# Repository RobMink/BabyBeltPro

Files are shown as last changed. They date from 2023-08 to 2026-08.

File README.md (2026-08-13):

# BabyBeltPro
BabyBelt Pro (V2.6, see branches for V1, V2, or v2.5)

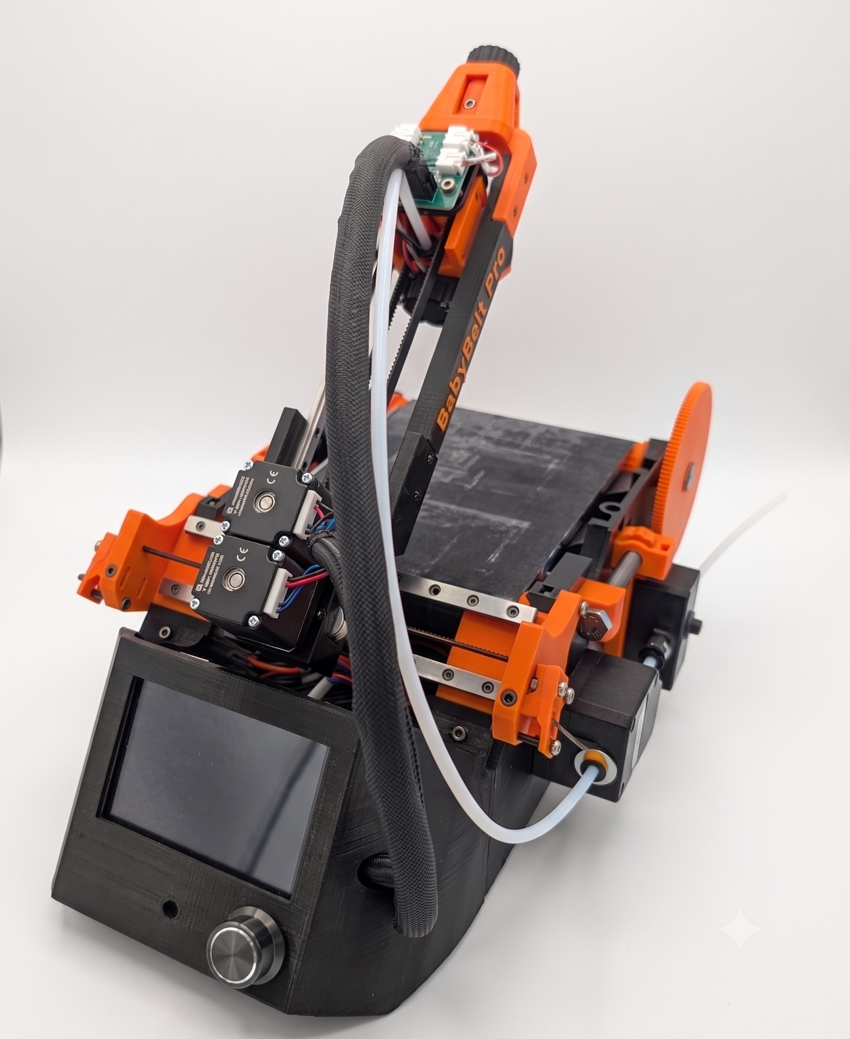
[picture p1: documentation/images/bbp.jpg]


 Whats new for v2.6
   - Changed from 3 MGN7H rails (2X 1Y) to 1 MGN9C(Y) and 1 MGN12C(X)
   - Removed 2mm screws (2.5s still needed for steppers and some hotend parts)
   - Added M3x6 BHCS (Y Gantry to MGN12 rail) and M3x30 SHCS (new X gantry to frame)
   - enhanced X gantry components for increased stability
       - X gantry now uses heatsets M3x4x5 (Voron style)
       - Backwards compatible with 2.5 BOM rails (mgn7H)
   - Improved hole and screw insertion patterns for easier installation on Y axis
   - Revised X/Y stepper mounting for easier install/maintenance

## The Printcepts Ethos
Remember when you didn't need 30 different types of screw to build your 3D printer? Printcepts remembers...  
We strive for a minimalist approach and don't go adding hardware "just because". If there is a screw that isn't an M3x10 or M3x20 SHCS we've got a very good reason for it!  
Printcepts started with a concept of taking parts you had lying around and making use of them. We want to thank everyone who gave us feedback, who wanted us to improve and we took that to heart! At it's core the Baby Belt Project will have its roots in re-using parts and being affordable. That's why we  

## Slicers that support Belt Printing

- [OrcaSlicer Nightly _belt build](https://github.com/OrcaSlicer/OrcaSlicer/releases/tag/nightly-builds) 
  - A HUGE THANK YOU goes out to Discord user and belt printing community member [@harrierpigeon](https://github.com/HarrierPigeon) for taking on this task. Early support for belt/infinite Z printers is well underway and has been added as an official branch with nighties.
  - Visit the link above and find the correct build for your platform that has _belt at the end.
  - A Princepts BabyBeltPro Klipper Firmware profile should be included within a couple days of 6/25/2026.
- [Kirimoto](https://grid.space/kiri/)
- [IdeaMaker](https://www.raise3d.com/ideamaker/)
- [BlackBelt Cura](https://blackbelt-3d.com/download-software/)* (We are not currently working on a profile for this slicer, mentioned simply as a potential option)
- [Command Line Blackbelt Cura](https://www.autodrop3d.com/blackbelt-slicer.html)* (See above)

## Printing your parts

Refer to our [Printed Parts Guide](/documentation/printed_parts_guide.md)

## Resources

| Links | Description |
|---|---|
| [BabyBelt Pro v2.6 Build Kit by LDO and West3D](https://west3d.com/products/baby-belt-pro-v2-5-complete-diy-belt-printer-kit-by-ldo-systems-and-west3d) | Purchase an all-in-one kit to get your BabyBelt built! * **
| [BabyBelt Pro v2.6 Build Kit By LDO](https://kb-3d.com/store/ldo/10320-ldo-babybelt-pro-v26-belt-printer-kit-6975415159855.html)  | Now Available at KB-3D! |
| [Documentation Index](./documentation/readme.md) |  Listing of most recent guides |
| Canuck Creator BabyBeltPro v2.6 build stream [Part 1](https://www.youtube.com/watch?v=DY8zT4xcWCY) [Part 2](https://www.youtube.com/watch?v=IuilQai8yGI) [Part 3](https://www.youtube.com/watch?v=38l1KDUIX3I) | Thank you to [Canuck Creator](https://www.youtube.com/@CanuckCreator) for all the doc feedback! |
| [Mods](documentation/Klipper/mods/) | Current Mods for the BabyBelt Pro (Includes information on Klipper) |
| [Printcepts Website](https://www.printcepts.com/) | Find out about other Printcepts Projects |
| [Printcepts Serial Number Registry](https://serials.printcepts.com/) | Take a look at the Printcepts Printers Serial registry |

| [Patreon](https://www.patreon.com/Printcepts)                | Help support Projects like this one!                                |
| [YouTube (RobMink)](https://www.youtube.com/c/robmink)       | Current home of Printcepts Video Content                            |
| [Discord](https://discord.gg/NTDZMsCwXh)                     | Join us for fun times or help with your build                       |
| [Facebook](https://www.facebook.com/groups/632751915097010)  | Kind of Inactive      |
| [Original BabyBelt Project](https://github.com/RobMink/BabyBelt)       | If you are looking for the Original Baby Belt, check here           |
| [GoFundMe for Belt Support in OrcaSlicer](https://www.gofundme.com/f/get-3d-belt-printers-into-orca-slicer)                             | We and the belt printing community would love this to be a reality  |

\* - Printed Parts not included

\** - Kit Electronics are fully functional with Marlin firmware.  For Klipper installs a user supplied compute module (pi, etc.) is required.

Hey we're now making it easier to see what changed and when!  
Check out our [Change log](/documentation/CHANGE-LOG.md)!

Non-commercial, Att.  
Printcepts  
email me: rob (at) printcepts.com

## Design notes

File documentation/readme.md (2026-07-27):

# Documentation Index

| Document | Description|
|---|-|
| [BBPv2 Build Guide](./bbpv2_build_guide.md) |START HERE!!!! 
| [Bill of Materials - v2.6 (June 2026 and later kits)](https://docs.google.com/spreadsheets/d/1v36plWF4jhTKyU7lcRmKtOrlq0xkhAmYc6CiN3XZ0d4/edit?usp=sharing) | What you need to build your own Baby Belt Pro 
| [Bill of Materials - v2.5 (May 2026 and earlier kits)](https://docs.google.com/spreadsheets/d/19PbR3nFbQ4-eIOTU0kmoTl5-mHv_KsTnUdfFXekWg-I/edit?gid=0#gid=0) | 
| [2.6 to 2.5 BOM Comparison](https://docs.google.com/spreadsheets/d/1kGRp7HetTHD1QJIhhra-hTphuUvGR_UmELGdN8hx2xM/edit?pli=1&gid=0#gid=0) | Blue-common, Red-2.5, Green-2.6.  Useful for upgrade/rebuild
| [Belt Assembly Instructions](./belt_guide.md) |How to create your own custom belt.
| [Printed Parts Guide](./printed_parts_guide.md) |Read the build guide to be sure you know what to print for your build.
| [Guided Firmware](./Guided_Firmware_Readme.md) |Updates planned
| [Klipper UART connection guide](./Klipper/mods/uart_connection.md) | Connect your Pi to your Mini E3 Inside the tub, keep it pretty.
| [Slicer Setup Guide](./slicer_setup_guide.md) |Instructions for importing supplied profiles into belt slicers
| [Loop Printing Guide](./loop_printing_guide.md) |Use M808 to easily print the same object multiple times
| [Legacy Build Instructions](https://docs.google.com/document/d/1dYbbvt_AkUhesFwPe-TYXSqsQAuzoHFzMLlQnfHJwGQ/edit?usp=sharing) |Original v2 Google Doc guide from Rob.

| [Legacy Fabreeko Kit Guide](./Fabreeko_kit_build_guide.md)    |
| [Known Issues](./Known_Issues.md)                             |
| [Change Log](./CHANGE-LOG.md)                                 |

## Operation Docs 
[Calculate Max Build_Height](./Calculate_max_build_height.md) - Updating Y-axis max_position and using it to calculate max_height.

## Mods (ish)
- [Mods Folder](./Klipper/mods/)
- [BTT TFT35-E3](./Klipper/mods/TFT35-E3.md) * Stock Screen - Used in Marlin Mode on Klipper
- [BTT PiTFT50 Screen](./Klipper/mods/TFT50.md) * Klipper Only
- [degree Sensor Switch](./Klipper/mods/degree_sensor_switch.md) * Klipper Only
- [Raspberry Pi Boot/Splash](/Software/RaspberryPi/plymouth) * Raspberry Pi and other debian type systems

## Print Tests
- [95mm_wide_flat_test.stl](/STLs/Tools/95mm_wide_flat_test.stl) * Test Y_Offset and first layer squish
- [30deg EM Flow Test Block.stl](/STLs/Tools/30deg%20EM%20Flow%20Test%20Block.stl) * Calibrate Extrusion Multiplier / Flowrate with 30 degree gantry
- [45deg EM Flow Test Block.stl](/STLs/Tools/45deg%20EM%20Flow%20Test%20Block.stl) * Calibrate Extrusion Multiplier / Flowrate with 45 degree gantry

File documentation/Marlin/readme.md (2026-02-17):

# Programming/Tuning

>[!NOTE]
>This guide is pretty old but should still work for the most part.

The default build is Marlin, but Klipper is great!  A full klipper guide is TODO

For Marlin, download the pre-compiled firmware file that matches your situation.  [Marlin Firmware](/Software/Firmware/Marlin/) rename the file to firmware.bin and stick it on a FAT32 formatted MicroSD card  (Note that FAT32 format only supports 32 GB and smaller microSD cards or partitions on a bigger card smaller than 32GB.  If this is confusing find a SD card 16 GB or smaller and try that.

Stick the card into the printer main board on the side, then power up the printer by plugging it in and flipping the switch.  If all goes well a little blinking red light on the board will flash rapidly, the screen will turn on and go “No Printer Connected” in the upper right.

After 30 seconds or so the red light will change, the screen should now say BabyBelt Pro with the “No Printer Connected” prompt gone.

## TroubleShooting Flashing the Firmware
If you don't get any picture on the screen but you get a red light on the main board, verify the screen is plugged in correctly. 

If you get Ender3 on the screen and no “No Printer Connected” you did not flash.  Check the SD card for a firmware.cur file.  If you still have firmware.bin try formatting the card or a different card, then turn the printer off, install the card, power up and try again.

## Testing and Tune
Home your printer using the screen.  You should get a clean move Left, then down, then the belt will jiggle.
 If using a kit you should not need to adjust the motor currents, directions, or TMC bump sensitivity.  It is still strongly recommended to verify the motors do not get too warm when they are active and adjust as needed using the current adjustment in the menu.  Same with the Sensorless homing settings.  255 is most sensitive for homing, 0 is least.

Warm up the hot end and make sure the fan on the heatsink spins.  If it does not turn on immediately after 50 degrees turn off the printer and check your fan wiring.  No hot end fan can melt your printer.

After the warm up, see if the printer will push filament by loading and running the extruder.  

Test the parts cooling fan.

It is always a good idea to tune your extruder.  The default firmware is set up for a BMG, but it should be considered a good ball park if you want to get high quality prints.  
https://ellis3dp.com/Print-Tuning-Guide/articles/extruder_calibration.html

I would also recommend a PID tune.
https://marlinfw.org/docs/gcode/M303.html

On a belt printer the first lawyer squish is set with the Y axis, not the Z axis.  Because the printer is set to several gantry angles if your Y home is too aggressive the gantry can flex a little when homing causing your first layer to be too squished.  This can be offset by adjusting the sensitivity on the Y axis as well as setting an offset to your start Gcode.

You should be ready to push plastic with a test print now!

Default settings:

X steps 100
Y steps 100
Z steps 364
E steps (depends on your extruder!  420 ish for a bondtech style)

As always, the discord channel is here to help.  Just ask and Rob or someone in the community will respond.  Also, feed back is super helpful.  Don’t be shy!  If you have a question it means that you are awesome and found a new opportunity to teach something, or the documentation is lacking(usually this).  I know this is a long manual and it is also possible that an error was made in my writing or your reading, so reread this and let us know!

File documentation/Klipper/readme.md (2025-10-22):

Good, Good... let the speed flow through you...

This guide was written using the SKR mini E3 V3. For users flashing Klipper for the first time, please see the manufacturer's documentation [here](https://github.com/bigtreetech/BIGTREETECH-SKR-mini-E3/blob/master/firmware/V3.0/Klipper/README.md)
Additionally, it is recommended to use a pre-built Klipper image to have many of the Klipper related items preinstalled and preconfigured for you. We don't judge if you use Fluidd or Mainsail either 😉

# Where did you get your kit? / Which Kit do you have?

| Self Sourced | Fabreeko | 
|:---|:---:|
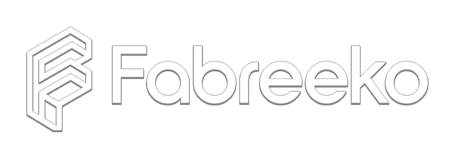
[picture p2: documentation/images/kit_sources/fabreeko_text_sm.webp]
Fabreeko
| Self Sourced |  |

# Pre Built Firmware Images  
| Board | Klipper Version | USB  | Serial |
|:---|:---:|:----:|:---:|
| SKR Mini E3 V3 | v0.12.0-416 | [klipper_USB.bin](../../Software/Firmware/klipper/binary/SKR%20Mini%20E3%20V3/klipper_USB.bin) | [klipper_uart_PA3_PA2_250000_baud.bin](../../Software/Firmware/klipper/binary/SKR%20Mini%20E3%20V3/klipper_uart_PA3_PA2_250000_baud.bin) |

# 🧭 Y Offset Calibration Macro

This macro helps you fine-tune your **Y offset** for accurate bed alignment on belt or traditional 3D printers running **Klipper**.

---

## 📂 File Inclusion

In your `printer.cfg`, include this file: [Y_OFFSET.cfg](../../Software/Firmware/klipper/options/Y_OFFSET.cfg)

```ini
[include Y_OFFSET.cfg]
```

---

## ⚙️ Temporary Extruder Adjustment

Temporarily allow cold extrusion by setting:

```ini
[extruder]
min_temp: 0
```

---

## 🧰 Required Test Object

Load the calibration STL from: [95mm_wide_flat_test.stl](../../STLs/Tools/95mm_wide_flat_test.stl)

---

## 🧩 Preparation Steps

1. **Start with no offset:**

   ```ini
   [homing_override]
   ...
   SET_GCODE_OFFSET Y=0
   ```

2. **Ensure:**
   - No filament loaded  
   - Extruder and bed temperature at **0 °C**  
   - Empty toolhead  

3. Slice and load the **flat_test** object.

---

## 🧾 Calibration Process

While printing the test object:

- Run the macros from `Y_OFFSET.cfg`  
- Use the **Y_PLUS** and **Y_MINUS** macros to adjust until the nozzle just **barely touches the belt** (or bed surface).  
- Once satisfied, **update your `printer.cfg`** with the final Y offset value.

---

## 🔥 Final Tuning (with Heat and Filament)

1. Re-slice the test object using your filament’s normal printing temperatures.  
2. Load filament.  
3. Run the print again and fine-tune the **Y offset** using the macros.  
4. Update and save the tuned value in your `printer.cfg`.

---

## 🧮 Macro Reference

| Macro Name | Adjustment | Description |
|---|---|---|
| `Y_PLUS1` | +0.1 mm | Coarse increase |
| `Y_PLUS01` | +0.01 mm | Medium increase |
| `Y_PLUS005` | +0.005 mm | Fine increase |
| `Y_MINUS1` | −0.1 mm | Coarse decrease |
| `Y_MINUS01` | −0.01 mm | Medium decrease |
| `Y_MINUS005` | −0.005 mm | Fine decrease |

---

## ✅ Summary

Once the optimal offset is found:
- Update `printer.cfg`
- Save and restart Klipper
- Enjoy consistent first-layer performance 🎯

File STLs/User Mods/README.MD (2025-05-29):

# User Mods

Here you will find modifications for the Baby Belt Pro that have been shared with us, and in turn we want to share them with all of you!  

### Madeline (On BabyBelt Discord)  
- [Locking Y Tensioner Nut](./Madeline/Locking%20Y%20Tensioner%20Nut)

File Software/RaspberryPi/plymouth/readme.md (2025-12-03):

# Raspberry Pi boot screen for BabyBeltPro

This is a `plymouth` theme to really jazz up your BabyBeltPro.

- [Hardware Required](#hardware-required)
- [Install Steps](#install-steps)
- [Troubleshooting](#troubleshooting)
- [Errata](#errata)
- [Credits / License](#credits--license)
- [AI Disclosure](#ai-disclosure)

## Hardware Required
- Raspberry Pi
  - _other SBCs / computers **should** work, provided they run a debian derived linux or support `plymouth`_
- BigTreeTech Pi TFT50
  - Any other screen will work, if it shows you output from your linux machine
  - Resolutions might be wonky? This hasn't been tested on anything else (except a 4k monitor)
  - But really, why wouldn't you just use the TFT50? There is already an [excellent mod](../../../documentation/Klipper/mods/TFT50.md)

## Prerequisites
You have a functioning system that display output on boot.
Ideally, this would be a Raspberry Pi with TFT50, that displays boot messages, and takes you some place useful like KlipperScreen. 

You are willing to potentially b0rk your system. Seriously, maybe have a backup, or at least the (unearned?) confidence to trust this code to make a bunch of changes to your boot environment. #yolo

## Install Steps
There are two ways of doing this, the easy **DANGEROUS** way, and the harder, slightly less dangerous, way.

##### Easy Way:
From your RaspberryPi, login via SSH or local terminal and run:

`curl -s https://raw.githubusercontent.com/RobMink/BabyBeltPro/main/Software/RaspberryPi/plymouth/install.sh | bash`

##### Slightly Harder way:
Copy `install.sh` from this directory to your RaspberryPi, then 

`bash ./install.sh`

## Troubleshooting
As things comes up, the answers will be added here.

## Errata
_Nothing yet... just a place for random odds/ends_

## Credits / License
The plymouth theme is a wholesale copy with minor tweaks of HerbFargus' [Retropie Theme](https://github.com/HerbFargus/plymouth-themes/tree/master)
This work is available under GPLv3, same as the BabyBeltPro project. 

## AI Disclosure
Generative AI was used in the creation of the images. The originator [mrchristian / hanzov69](https://github.com/hanzov69) with full commercial/unrestricted usage rights, and releases them under the same license(s) covering the BabyBeltPro project.

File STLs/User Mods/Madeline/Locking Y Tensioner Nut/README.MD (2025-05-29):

# Locking Y Tensioner Nut

- [Step File](./BBProV2_RockMonsterNo1YTentionerNut%20Locking.step)
- [3MF](./BBProV2_RockMonsterNo1YTentionerNut%20Locking.3mf)

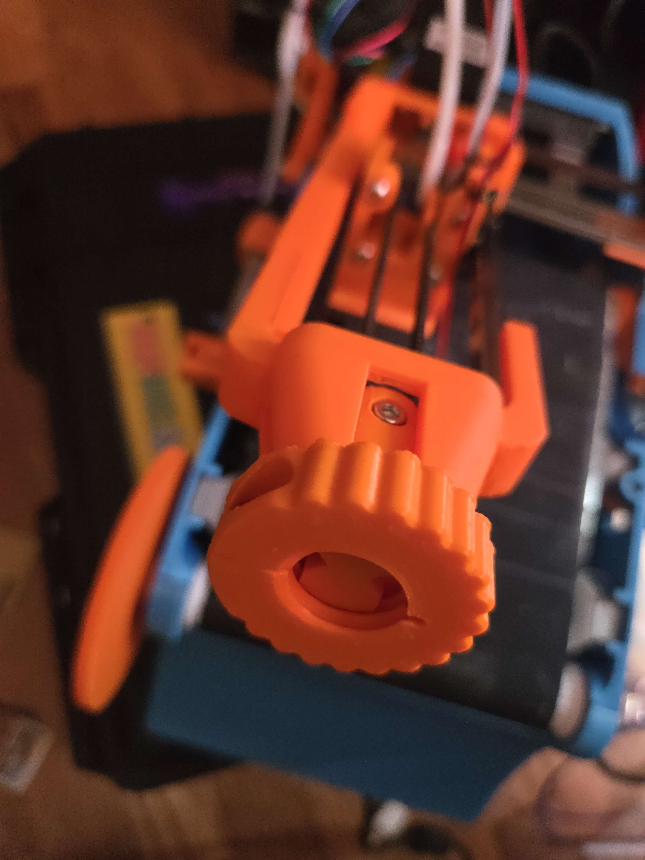
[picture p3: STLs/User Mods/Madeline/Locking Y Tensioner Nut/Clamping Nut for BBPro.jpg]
Image of the Locking Nut in use


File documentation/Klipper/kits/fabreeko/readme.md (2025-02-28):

# Fabreeko Baby Belt Pro Kit

Available for purchase: [Here](https://www.fabreeko.com/products/baby-belt-pro-kit-by-honeybadger?_pos=1&_psq=baby&_ss=e&_v=1.0)  

Build Manual: Soon™

Grab our [Klipper config](../../../../Software/Firmware/klipper)

Once you get set up, the first thing you need to do is decide which screen to use and whether or not you want to use our new degree detection switch

Enabling them with our pre-built config is as easy as uncommenting a line! (PiTFT50 requires additional configuration/setup outside of printer.cfg)

[TFT35-E3 Screen](../../mods/TFT35-E3.md) - The Stock screen that comes with the Baby Belt, to be used in Marlin Mode.  
[BTT PiTFT50](../../mods/TFT50.md) - Use KlipperScreen with a TouchScreen  
[Degree Sensor Switch](../../mods/degree_sensor_switch.md) - Let your printer detect if you are at 30° or 45°   
[UART connection](../../mods/uart_connection.md) - Keep things clean with wires internal between your Pi and board!  
[XL Mod](../../mods/baby_belt_pro_XL.md) - Baby Belt Pro... but BIGGER!  
[BTT Smart Filament Sensor 2.0](../../mods/BTT_SFS_2.md) - Filament Runout sensor.  

If you have any issues you can check our [Known Issues](../../../Known_Issues.md) page or reach out to us on [Discord](https://discord.gg/nVmeNJJSH2)

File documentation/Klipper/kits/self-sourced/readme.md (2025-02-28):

At this time since we cannot have every motor tuning sorted out, you can use the existing [Klipper configuration](../../../../Software/Firmware/klipper) and modify the existing entries for driver_SGTHRS for each axis. 

You can also choose which of our additional modifications to use

Enabling them with our pre-built config is as easy as uncommenting a line! (PiTFT50 requires additional configuration/setup outside of printer.cfg)

[TFT35-E3 Screen](../../mods/TFT35-E3.md) - The Stock screen that comes with the Baby Belt, to be used in Marlin Mode.  
[BTT PiTFT50](../../mods/TFT50.md) - Use KlipperScreen with a TouchScreen  
[Degree Sensor Switch](../../mods/degree_sensor_switch.md) - Let your printer detect if you are at 30° or 45°  
[UART connection](../../mods/uart_connection.md) - Keep things clean with wires internal between your Pi and board!  
[XL Mod](../../mods/baby_belt_pro_XL.md) - Baby Belt Pro... but BIGGER!  
[BTT Smart Filament Sensor 2.0](../../mods/BTT_SFS_2.md) - Filament Runout sensor.  

If you have any issues you can check our [Known Issues](../../../Known_Issues.md) page or reach out to us on [Discord](https://discord.gg/nVmeNJJSH2)

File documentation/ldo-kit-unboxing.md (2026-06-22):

  
# BabyBelt Pro V2.5 West3d/LDO Motors Kit Unboxing
BabyBelt Pro V2 by RobMink, kit compiled and offered by West3D and LDO Motors
>[!NOTE]
>This is the unboxing of a v2.5 BOM kit.  Screws and rails will differ for kits sold after June 2026.

Jump To...

- [BOM and Box](#bom-and-box-opening)
- [Motor Kit Box](#Motor-Kit-Box)
- [Linear Rail Box](#Linear-Rail-Box)
- [Extruder Box](#Extruder-Box)
- [AC Adapter Box](#AC-Adapter-Box)
- [Heatbed Box](#Heatbed-Box)
- [Motion and Fasteners Box](#Motion-and-Fasteners-Box)
- [Electronics Box](#Electronics-Box)
- [BTT TFT35-E3 Box](#BTT-TFT35-E3-Box)
- [SKR Mini E3 V3 Box](#SKR-Mini-E3-V3-Box)
- [Hotend Box](#Hotend-Box)
- [AC Cord](#AC-Cord)
- [Power Jack](#Power-Jack)
- [Belt](#Belt)

## BOM and Main Box
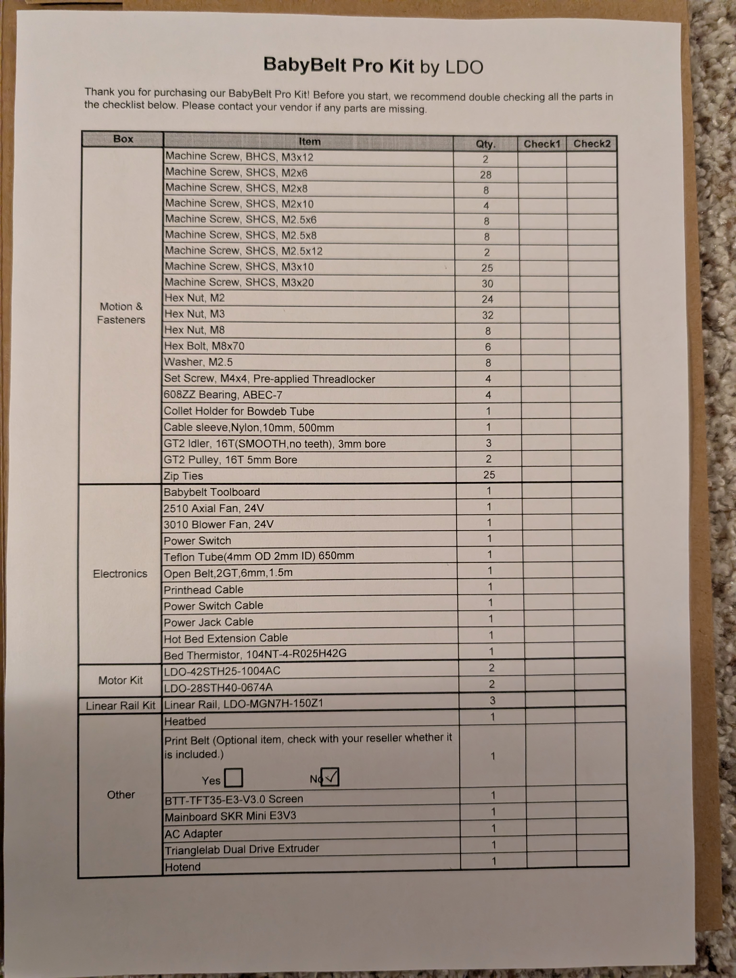
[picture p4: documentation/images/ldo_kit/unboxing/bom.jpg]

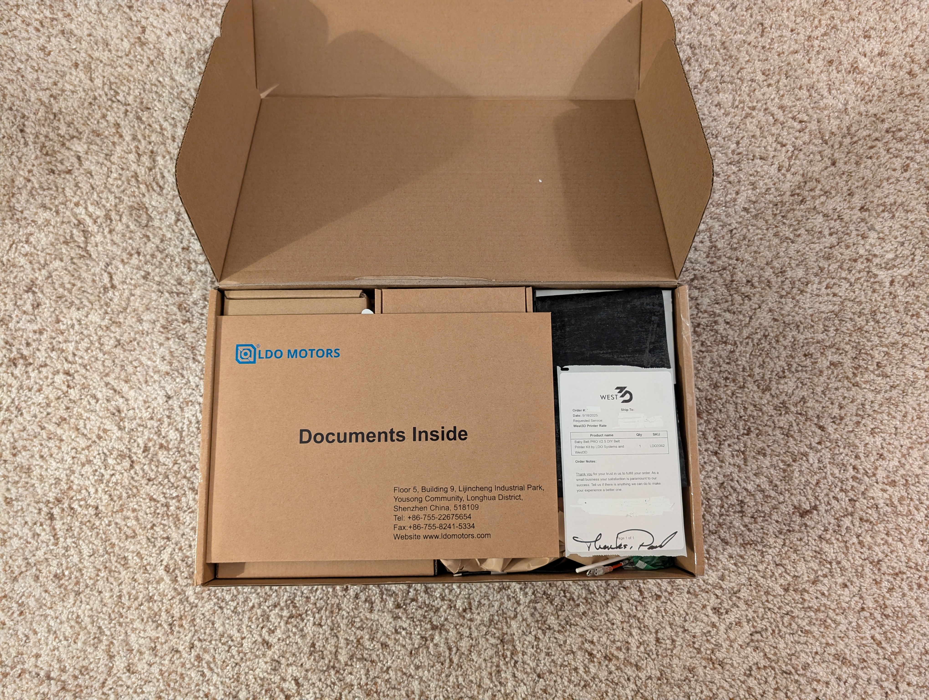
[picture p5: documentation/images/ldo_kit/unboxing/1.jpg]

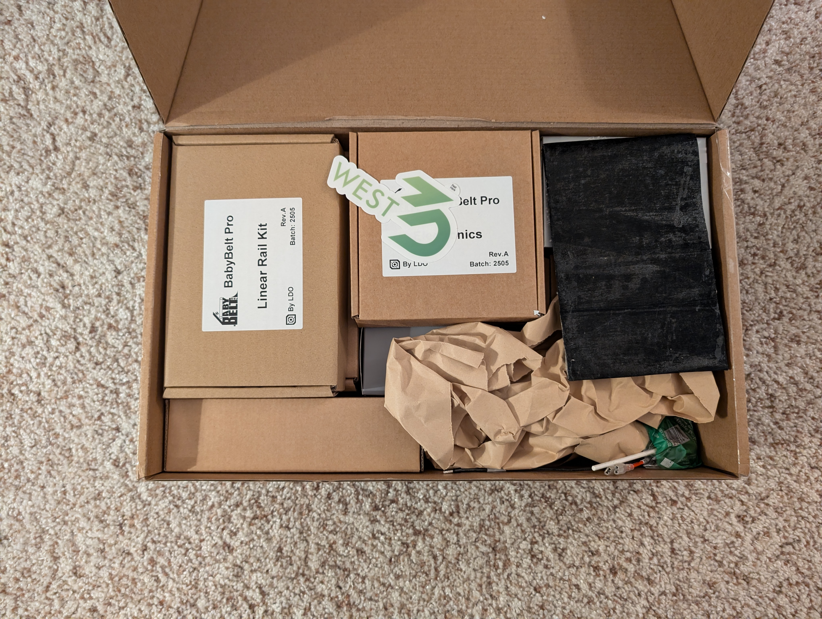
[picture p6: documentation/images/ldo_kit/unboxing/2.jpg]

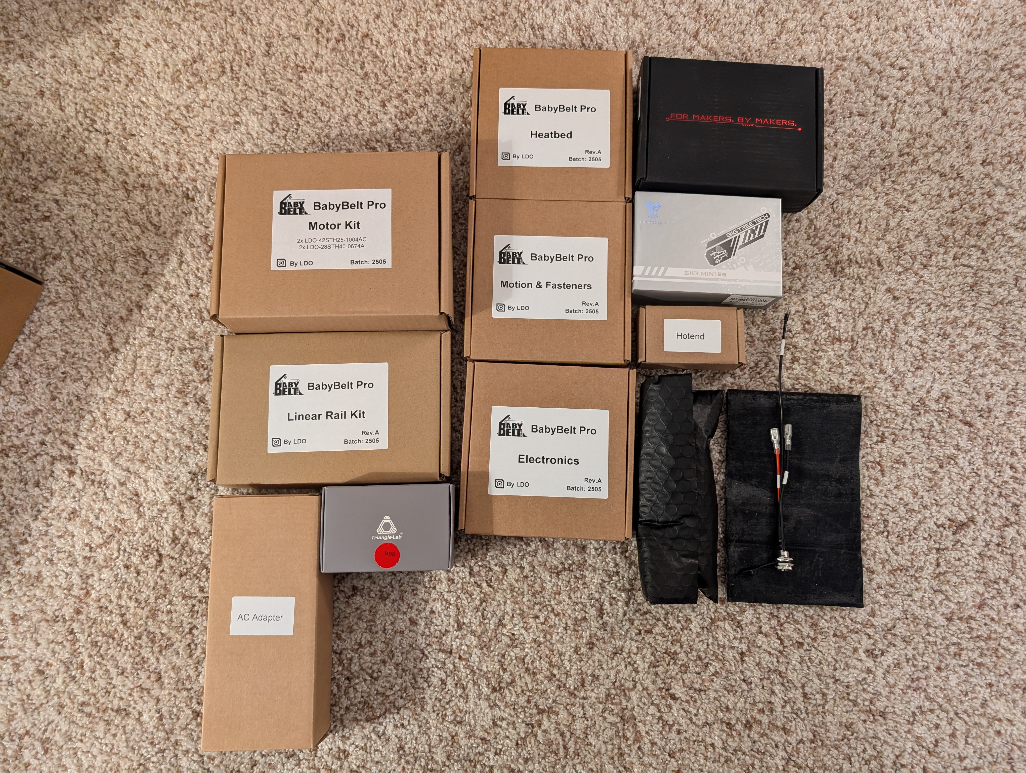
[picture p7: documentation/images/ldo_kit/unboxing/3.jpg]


[Jump to Top](#top)

## Motor Kit Box
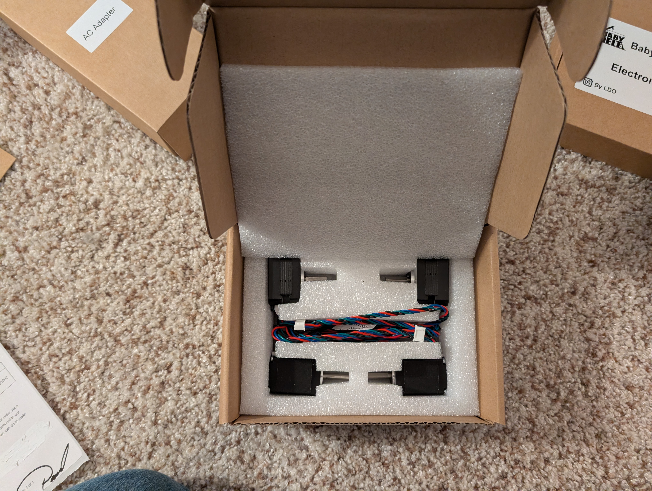
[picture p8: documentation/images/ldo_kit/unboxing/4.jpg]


[Jump to Top](#top)

## Linear Rail Box
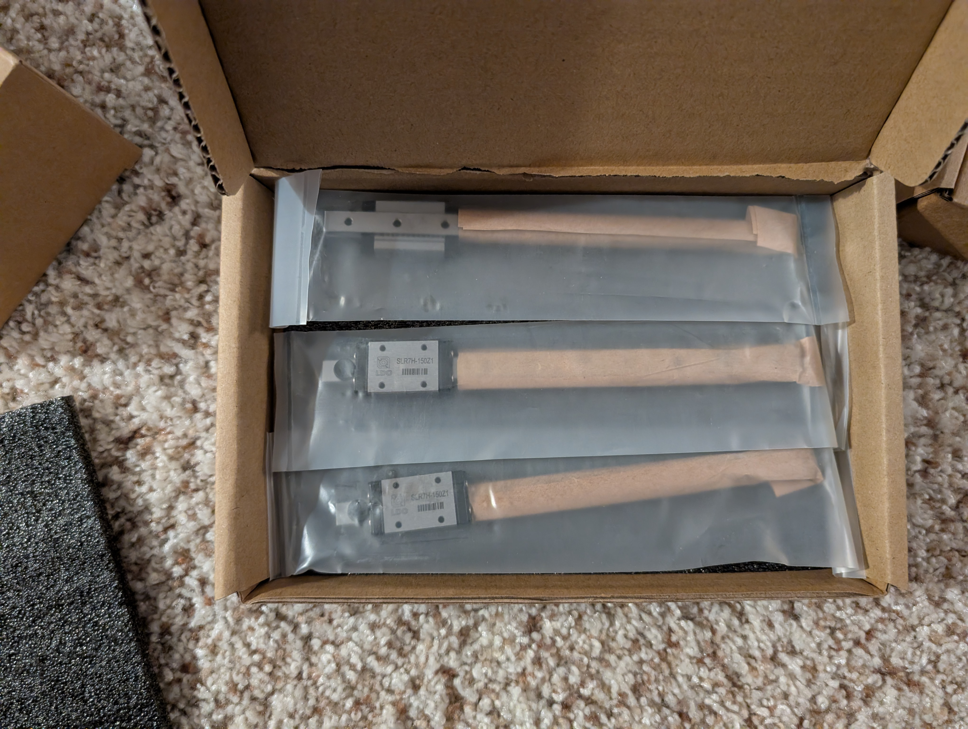
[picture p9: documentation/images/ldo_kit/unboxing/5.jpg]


[Jump to Top](#top)

## Extruder Box
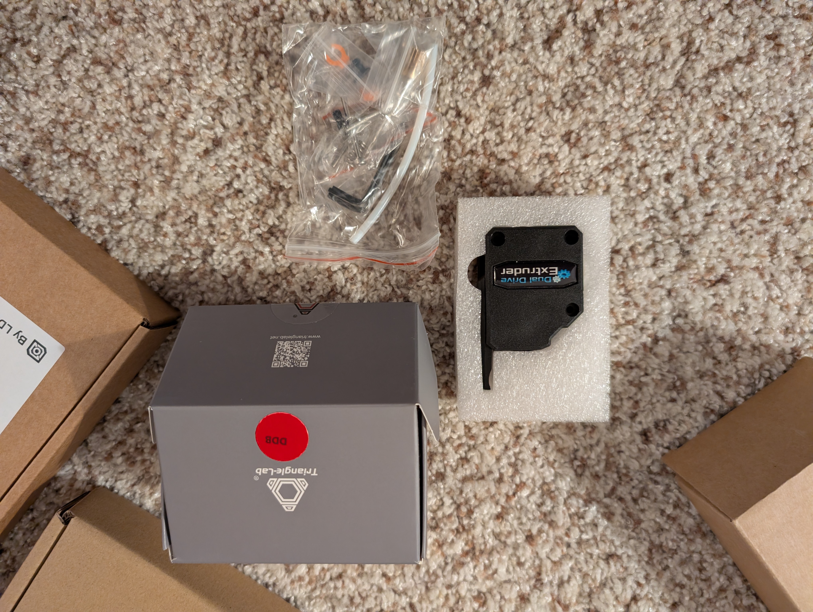
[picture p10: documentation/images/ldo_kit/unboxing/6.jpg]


[Jump to Top](#top)

## AC Adapter Box
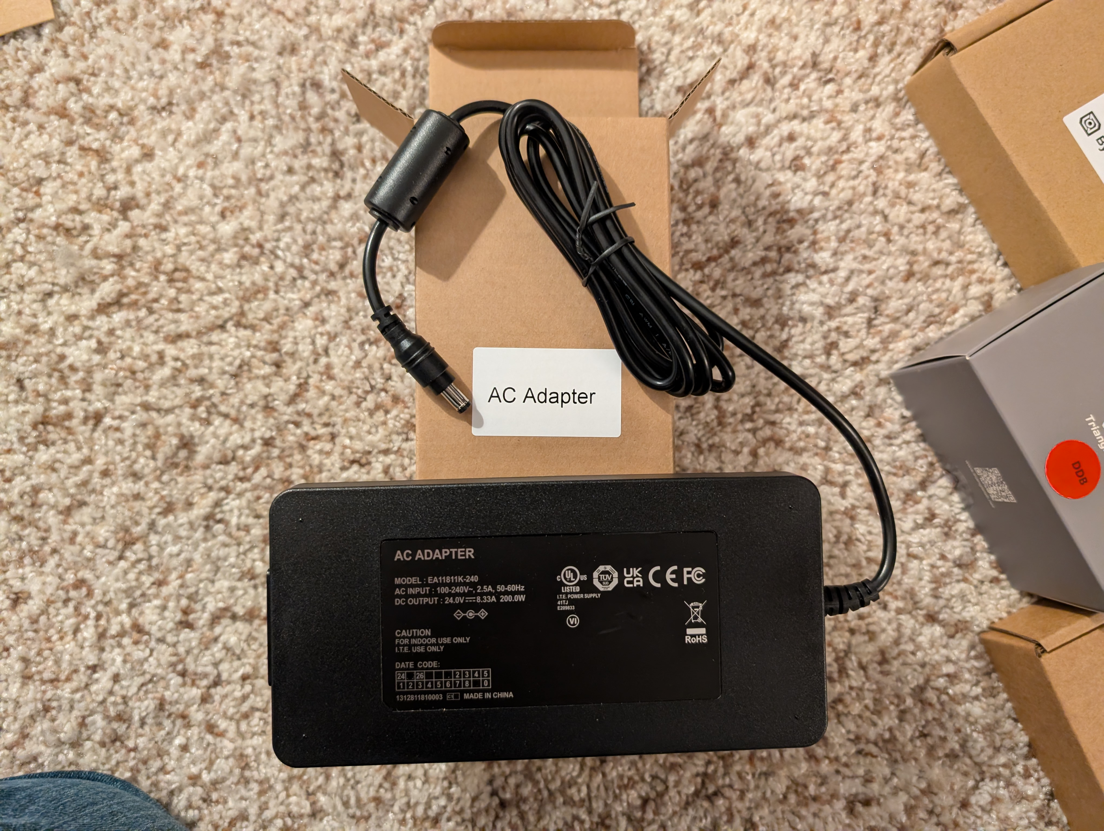
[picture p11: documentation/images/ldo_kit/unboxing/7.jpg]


[Jump to Top](#top)

## Heatbed Box
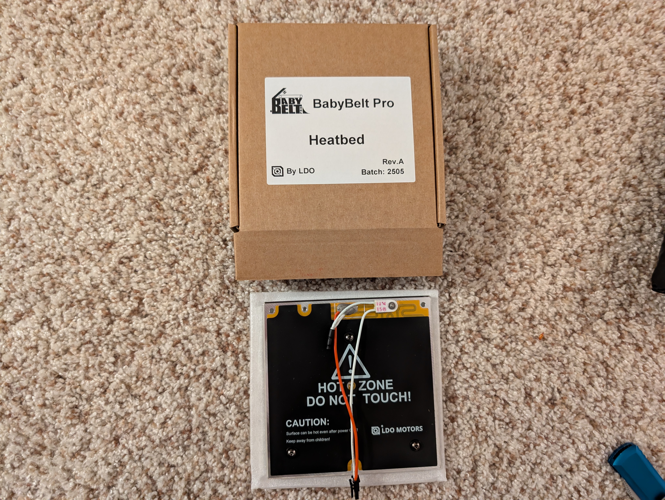
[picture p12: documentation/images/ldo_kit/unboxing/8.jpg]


[Jump to Top](#top)

## Motion and Fasteners Box
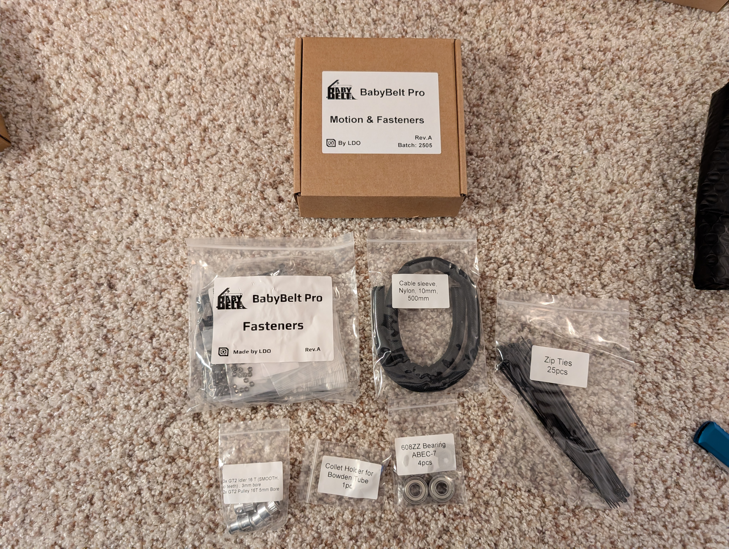
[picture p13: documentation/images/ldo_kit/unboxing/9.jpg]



[Jump to Top](#top)

## Electronics Box
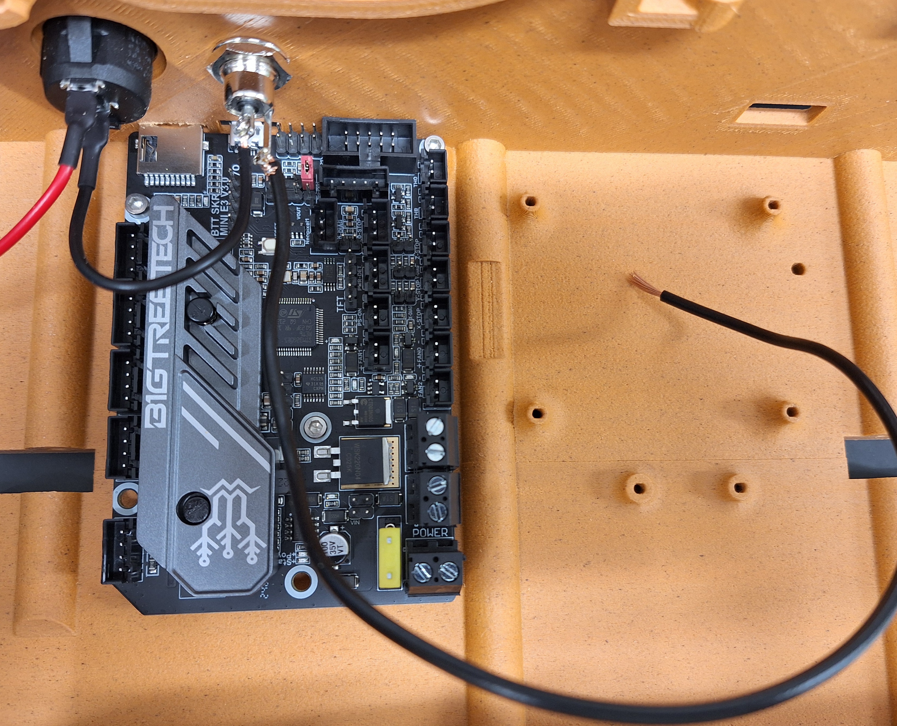
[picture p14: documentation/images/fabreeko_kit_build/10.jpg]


[Jump to Top](#top)

## BTT TFT35-E3 Box
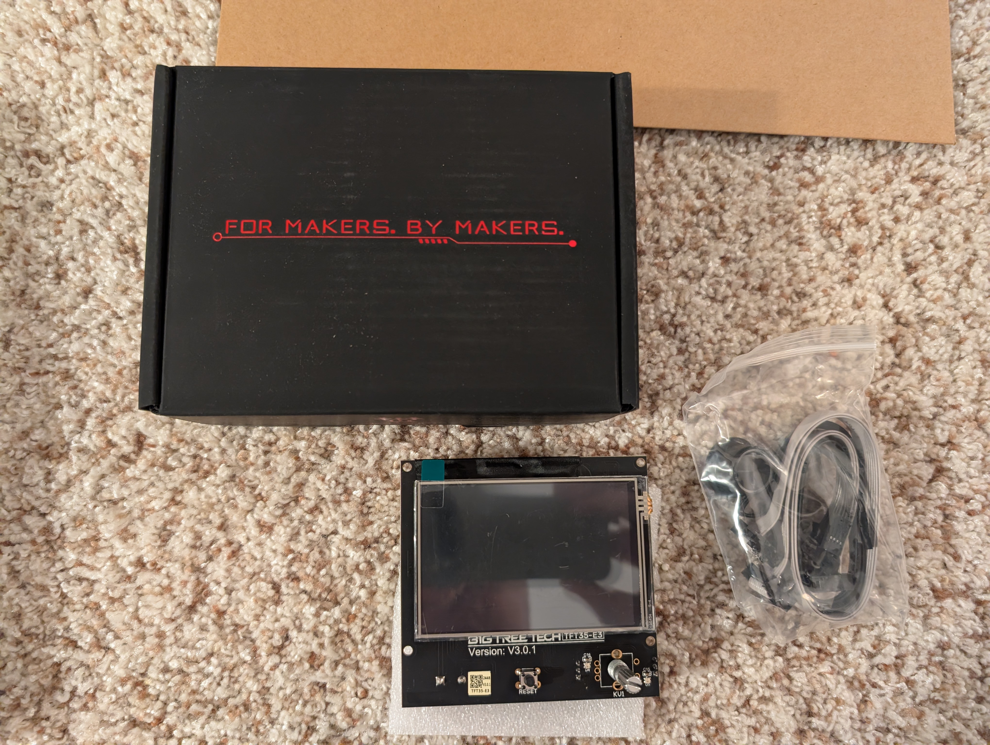
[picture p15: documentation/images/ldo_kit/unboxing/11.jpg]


[Jump to Top](#top)

## SKR Mini E3 V3 Box
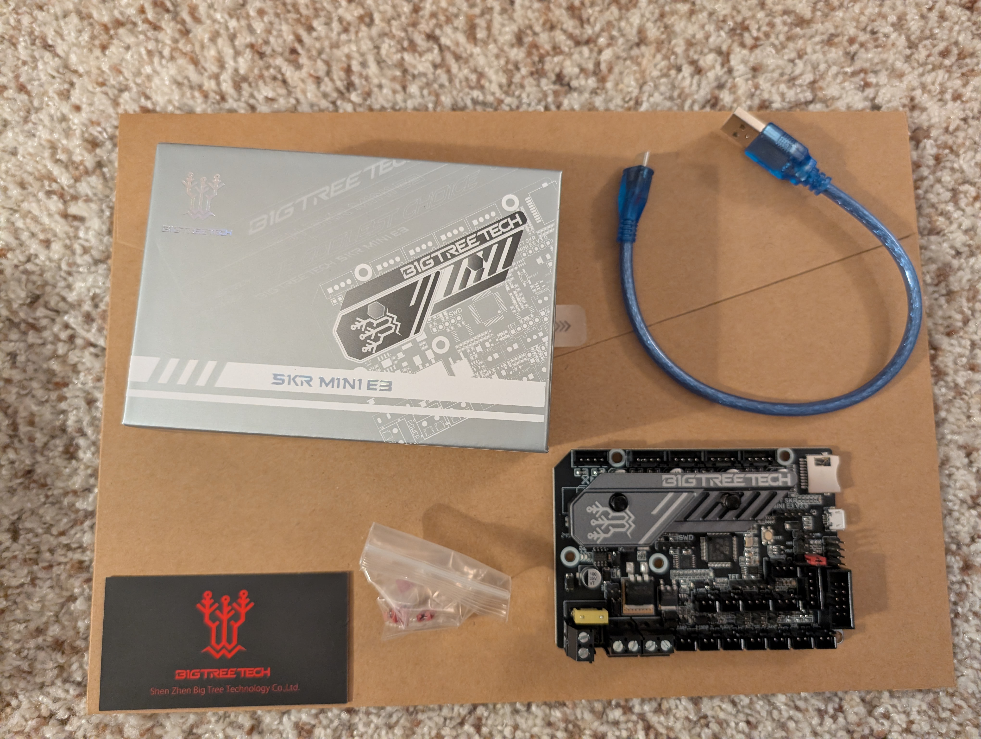
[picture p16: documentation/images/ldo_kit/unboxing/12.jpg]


[Jump to Top](#top)

## Hotend Box
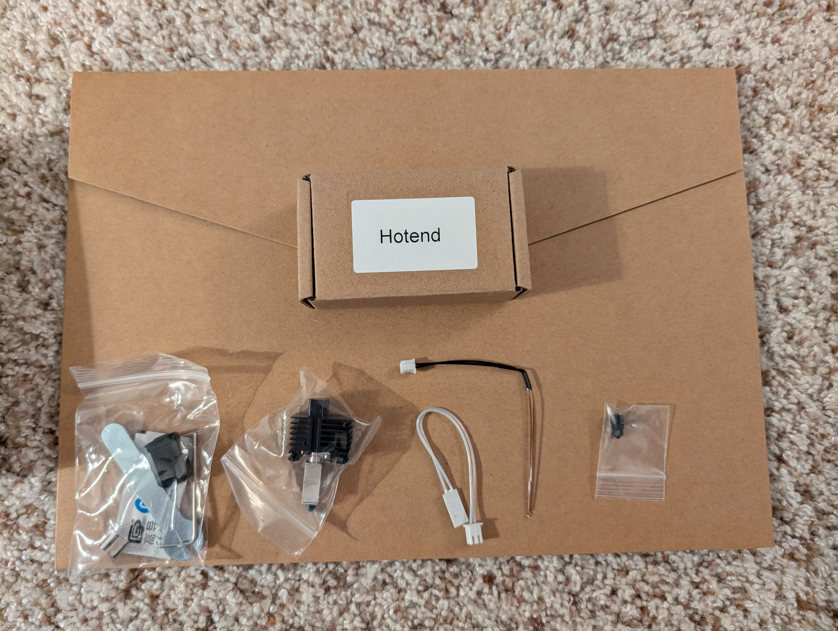
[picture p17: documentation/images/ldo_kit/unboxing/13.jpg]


[Jump to Top](#top)

## AC Cord
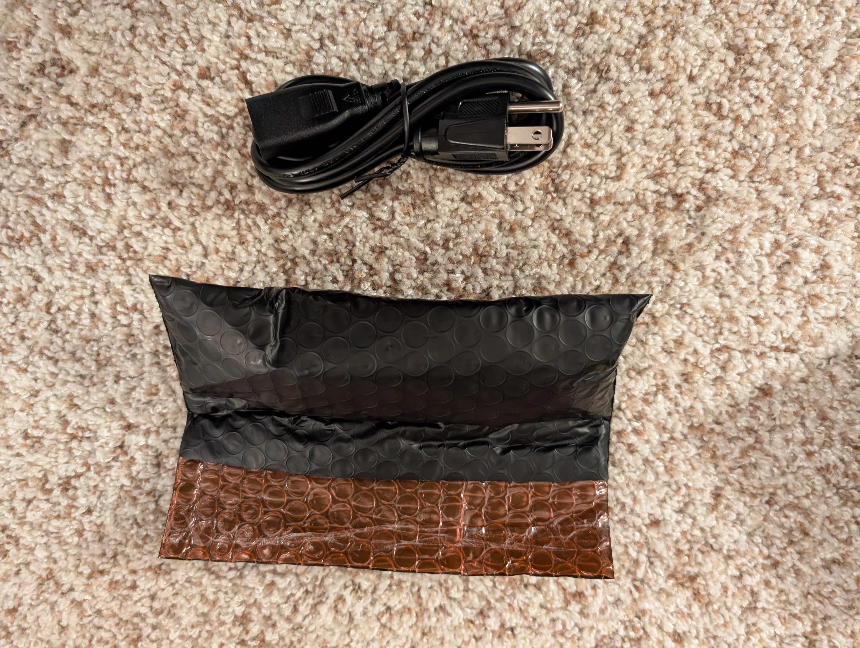
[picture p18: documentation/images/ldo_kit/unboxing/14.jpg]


[Jump to Top](#top)

## Power Jack
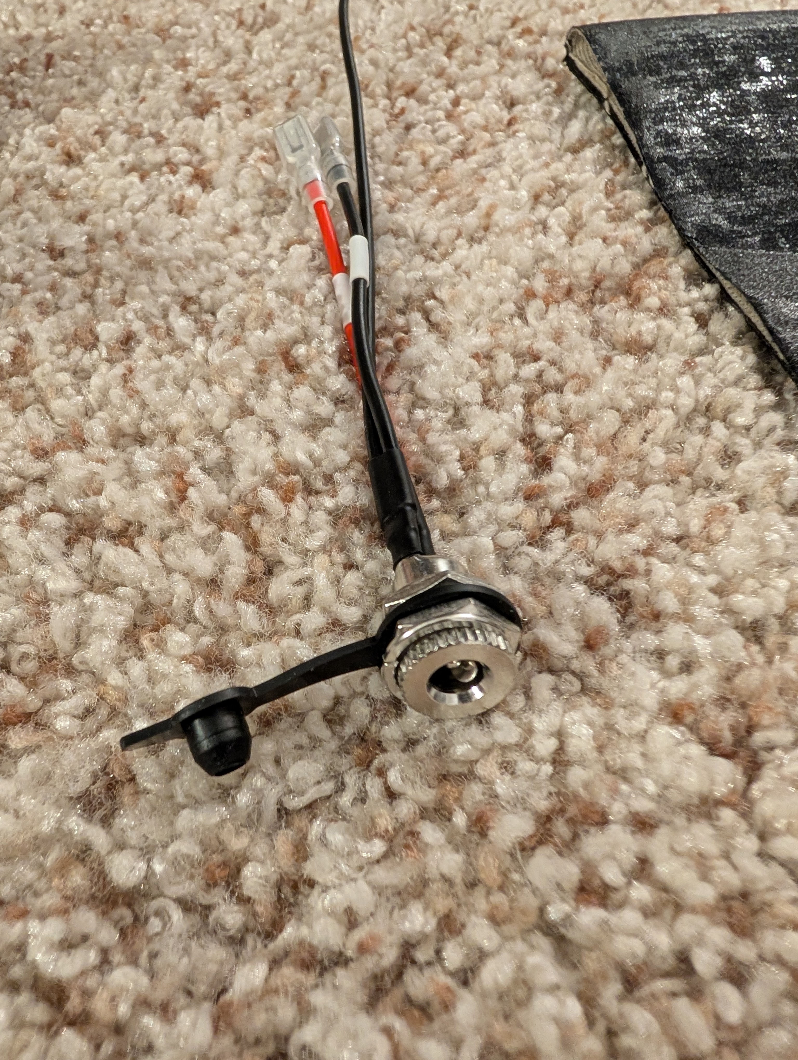
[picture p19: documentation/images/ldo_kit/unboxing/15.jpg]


[Jump to Top](#top)

## Belt
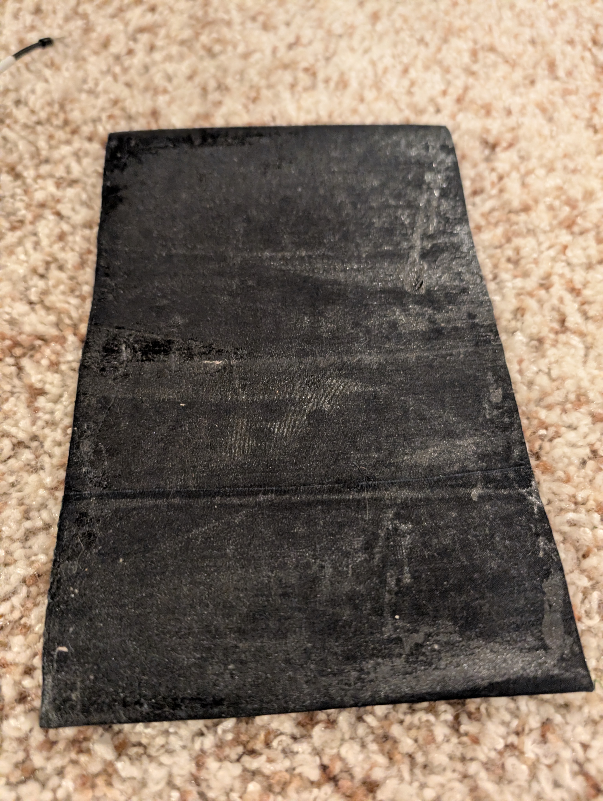
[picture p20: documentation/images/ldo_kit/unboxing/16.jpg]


[Jump to Top](#top)

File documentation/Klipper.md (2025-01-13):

# Klipper on BabyBeltPro

This guide was written using the SKR mini E3 V3. For users flashing Klipper for the first time, please see the manufacturer's documentation [here](https://github.com/bigtreetech/BIGTREETECH-SKR-mini-E3/blob/master/firmware/V3.0/Klipper/README.md)
If you are following this section, please use the configuration files from the [Angle Switch Included](../Software/Firmware/klipper/angle_switch_included) Klipper Folder
Additionally, it is recommended to use a pre-built Klipper image to have many of the Klipper related items preinstalled and preconfigured for you. We don't judge if you use Fluidd or Mainsail either 😉  

Table o' Contents
- [BOM Differences](#bom-differences)
- [Printed Part Changes](#printed-part-changes)
- [Degree Sensor Switch Wiring](#degree-sensor-switch)
- [Installing the Switch](#installing-the-switch)
- [Screen Changes](#screen-changes)
- [Validation](#validation)

## BOM Differences
- Remove BTT-TFT35-E3-V3.0 screen
- Add BTT Pi TFT50 (Preferrably v2.1)
- Add 1 Omron D2F-5L (or similar)
- Add 2x M2x10 Self Tapping Screws
- Add 3x M3x5x4 Heat set inserts
- Add 3x M3x14 SHCS
- Add 1x (300mm) Pi TFT Cable (Prefer Adafruit as the cable backer is shorter) 
  - Stock has a 5mm tall Backer, Amazon Special has 7mm Backer. You can trim this yourself if you are INCREDIBLY careful when both peeling up from the back and cutting, I take no responsibility if you damage your cable by modification.
- Approximately 160mm of 24AWG stranded wire
- JST-XH Female Crimp ends (SXH-001T-P0.6 or SXH-001T-P0.6N)
- JST-XH 3-wire housing (XHP-3)
- For the new X Belt Clamp (if the original BOM has not been updated)
  - 4 M3x10 (You can use whatever cap you like, I think BHCS looks best) * These are for the X Axis Belt Clamps
  - 4 M3x20 SHCS (These are to adjust your tension on both sides & to act as a pivot arm)
  - 6 M3 Normal Nuts

## Printed Part Changes
There are a few key differences in the assembly of the Baby Belt Pro for Klipper, the main differences are the front screen mount and a sensor switch. 

[Front Screen](../STLs/Frame/Mods/Klipper%20PiTFT50%20Screen/Klipper%20Screen%20Mount.stl)  
[Screen Cartridge](../STLs/Frame/Mods/Klipper%20PiTFT50%20Screen/Screen%20Cartridge%20-%20BTT%20PI%20TFT50%20v2%20cover.stl)

## Degree Sensor Switch
Take the 28AWG wire and strip a small portion of it, solder a wire to each of the outer legs of the switch as seen here.  
After you have connected them, add your crimp ends then gently twist the two wires to keep things nice and tidy. When you have reached the end of the wires, grab the JST 3 pin Wire housing and insert them in the right two spots if viewing the connector in a "pins up" orientation [see here](#xhp-3-wiring).   
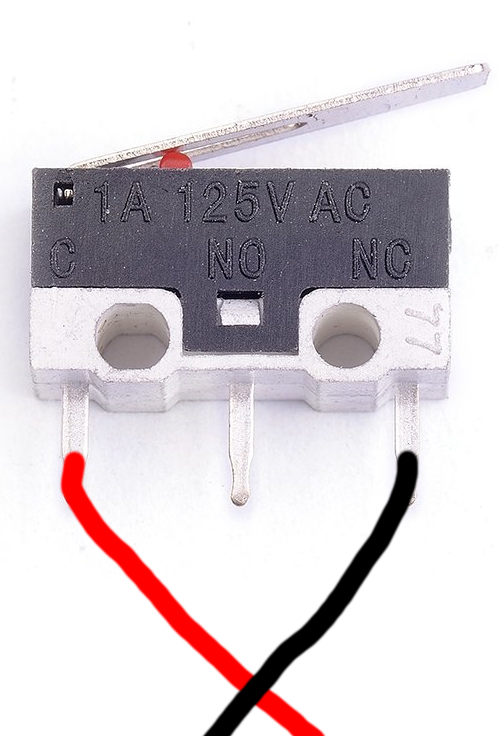
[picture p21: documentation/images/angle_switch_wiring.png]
Switch Wiring Image


## XHP-3 wiring

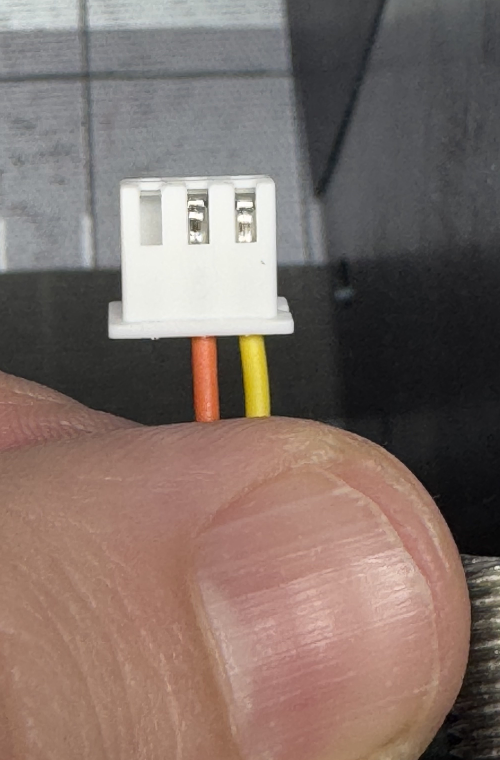
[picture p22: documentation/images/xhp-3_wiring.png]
XHP-3 image


## Installing the switch
Next, on [Side A](../STLs/Frame/BBProV25fl_Side-A.stl) if you are using an existing part, take the D2F-5L switch and place it so that the face of the plastic is aligned with the front face of the case and the protruding side of the lever is closer to you.  

Front View  
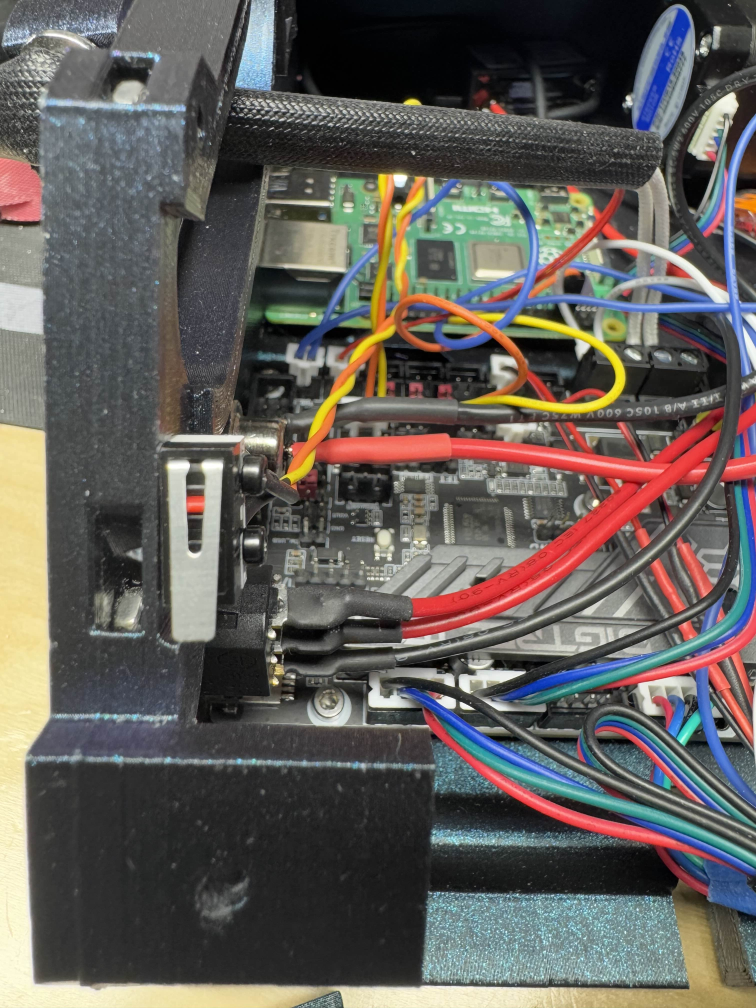
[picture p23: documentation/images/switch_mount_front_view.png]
Front View
  
Outside View  
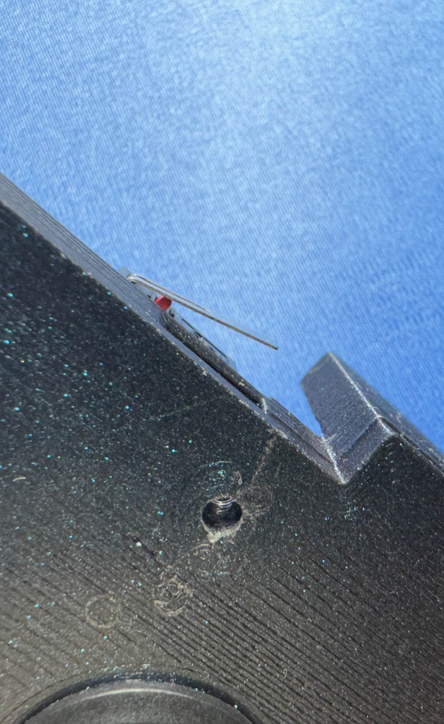
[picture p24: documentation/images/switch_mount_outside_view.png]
Outside View
  
Inside View  
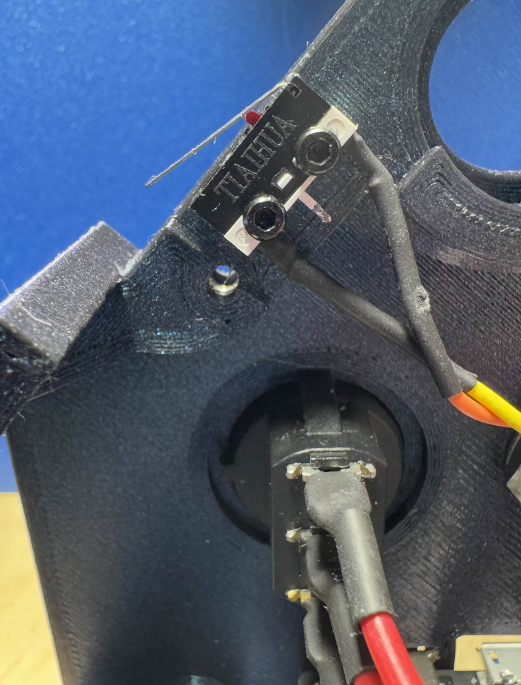
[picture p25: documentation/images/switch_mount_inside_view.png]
Inside View
  

Next take the other end of the wire, now crimped and in it's housing and plug it into the main board.  
We will be using the E0-STOP port highlighted here in green.  
SKR mini E3 V3 wiring diagram

## Screen Changes
Now we get to the fun part! First thing's first, take your [Screen Cartridge](../STLs/Frame/Mods/Klipper%20PiTFT50%20Screen/Screen%20Cartridge%20-%20BTT%20PI%20TFT50%20v2%20cover.stl) and set your heatset inserts into both sides, making sure to put them in as straight as possible.   
Next we grab your BTT Pi TFT50 v2.1 (If you have wheels instead of buttons it should still fit, but this was all tested/validated on a 2.1 with just buttons) and the TFT Cable. insert one end into the screen with the pins facing up and then ensure it is locked in place with the lever down.  
Then set your screen into the cartridge case cable side first, it is going to fold it a little and that's fine. Once you have the cable side set in, pull the excess of the cable through the opening in the back and gently set the other side down. It should fit fairly flush with 0 force (see below)  
BTT PiTFT in Cartridge  

Now we want to set it down on the screen so we can secure it to the cartridge. If you have the screws that came with it those are great! If you are like me and lost them... well I have good news! An M2.5 x6 BHCS will do the job just as good!
2.5mm x6mm BHCS

Pick a Corner to start with, then go diagonally across, up and then diagonally back down (see picture)  
Screen Cartridge Screw Order  

Congrats! You've got a Screen Cartridge! If this were some other guide we'd tell you to eat a piece of candy.   

Moving on, we need to slot our screen cartridge into the housing, this can be a bit tricky but if you are careful it will be just fine.  
We want to take the cable that is currently connected inside our "screen cartridge" and feel it into the bottom slot of the screen holder.  
Feed the cable into the mount

Next tuck it around the back of the screen and carefully hold it with a finger while you start inserting the screen cartridge into the holder. 
Hold the Cable, Insert Cartridge  

Once you have inserted past the flex cable section of the screen you can let go of the cable and insert the screen the rest of the way in. Your cable should be towards the back of the housing and you should have access to the buttons from the cutout in the cartridge as seen here  
Check Your Work Inserting the Cartrige  

Next you will want to screw in the side Screws (M3x14 SHCS Qty: 3) start with the side with a single hole and just get it started without screwing all the way in.  
Then insert the upper screw on the other side and get it started, finally the bottom screw on that same side. If everything lines up, tighten all three screws down.  
If they do not all insert, see if you have to push the cartridge ever so slightly to get it to line up, if not check that you inserted the cartridge correctly and that all of your heat sets are as straight as possible.

Finally, Insert the other end of the flex cable into the raspberry pi's display port, pull up on the tab without removing it, and insert the cable We want to ensure we are giving the pins the raspberry and then push the tab back down to lock the cable in place.  
Give those Pins the Raspberry!

## Validation
Fire up the machine and ensure everything works!

Firstly the screen should turn on immediately, and you should see the Pi booting up!   
If it is upside down, press the middle button on the bottom of the Pi TFT50 to rotate it.

If you see the Pi Booting up, but it stays at a terminal you need to install KlipperScreen. I suggest installing it via [KIAUH](https://github.com/dw-0/kiauh)

If you can see the interface, but touch is not working AT ALL you will need to modify your /boot/config.txt
```bash
sudo nano /boot/config.txt
```

and change the line that has   
```bash
dtoverlay=vc4-kms-v3d
```  
to  
```bash
dtoverlay=vc4-fkms-v3d
```  

If you have any other problems, open an issue here on GitHub or reach out on the Baby Belt Discord.

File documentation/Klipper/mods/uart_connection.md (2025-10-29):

# UART Connection Pi => SKR Mini E3 V3
So you want to keep more wires internal to the Baby Belt eh?
Great news! It's SUPER Simple!

Table o' Contents  
- [Wiring](#wiring)
- [Klipper Changes](#klipper-changes)
- [Pi Changes](#pi-changes)

## Wiring
Grab yourself a trio of wires (I used 26 AWG) roughly around 16cm in length  
and crimp both ends as Female Dupont connectors.
(You can also use individual female to female jumper wires if you have them from a breadboard kit)  

Next you will need to locate the pins in question and Remember that pins go to the opposite signal on either end of the cable.    
TX  => RX  (Orange)  
RX  => TX  (Yellow)  
GND => GND (Green)  

On a Raspberry Pi 3/4 you will be using pin 6 as GND (Green), pin 8 as TX (Orange), and pin 10 as RX(Yellow).
and on the SKR Mini E3 V3, you will need to use three of the TFT pins (see diagram)  

Diagram of Raspberry Pi Connecting via UART to SKR Mini E3 V3  
**Previous versions of this guide used only two wires (no ground).  Some users reported issues with serial connectivity without the interfaces sharing a common ground.  Thank you to discord user @Sturn for the find!

## Klipper changes
* Instructions are specific to SKR Mini E3 V3 with regard to Flashing
Klipper will need to be re-flashed to your board if it is already flashed. Be advised that you will use a microsd card that is formatted to fat32 and empty before we start
next build your Klipper firmware   

The Key difference here is we want to use Serial on USART2 PA3/PA2 for our communication interface (see below)
firmware menuconfig  

You will also need to update your mcu section of your printer.cfg to use   
```
/dev/serial0
```  
as your serial connection to the board. If for some reason /dev/serial0 isn't working, you can try /dev/ttyAMA0 if that is still not working, see the following Raspberry Pi Changes to enable the serial interface  

## Pi Changes
Remember that raspi-config command? No? Ok well we need to ssh into our Pi and run the following  
```
sudo raspi-config
```  
** This WILL Prompt you for your password, it's safe to enter it here **   
In this menu you will need to select option 3 Interface Options  
raspi-config serial enable 1  
then I6 for Serial Port  
raspi-config serial enable 2
You do not need to have the login shell accessible over serial
raspi-config serial enable 3
you *DO* however want the serial interface to be enabled  
raspi-config serial enable 4
press Ok on this confirmation screen, then press the right arrow twice to get to finish and press enter again to exit raspi-config
raspi-config serial enable 5
it will ask if you want to reboot now, go ahead and say yes
raspi-config serial enable 6

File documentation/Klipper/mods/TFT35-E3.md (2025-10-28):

# Using the TFT35-E3 on Klipper 

Please note that the TFT35-E3 is the stock screen that comes with the Fabreeko Kit  
As of this writing, you can simply uncomment / add 
```aiignore
[include options/BTT_TFT35.cfg]
```

to the top area of your printer.cfg 

For wiring, you just need to use the EXP Cable that comes with the screen and connect from EXP1 on the BTT SKR Mini E3 V3 to EXP3 on the BTT TFT35-E3  
No serial connection is required for this setup. If you want to add this to a already built / configured Klipperized Baby Belt, be sure to copy both "BTT_TFT35.cfg" **AND** "BTT_TFT35_menu.cfg"

You will need to change the mode of the screen from "Touch" to "Marlin".
Touch and HOLD your finger on the screen for 3 seconds.  Tap the icon labeled "Marlin", the screen will say Marlin Mode at the top.
To revert, repeat the process and tap the "Touch" icon.

Credit to Allen @West3D for getting this working!

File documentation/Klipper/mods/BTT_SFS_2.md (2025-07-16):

Table o' Contents
- [BOM](#bill-of-materials)
- [Wiring](#wiring)
- [Printed Parts](#printed-parts)
- [Assembly](#assembly)
- [Config Changes](#config-changes)

## Bill of Materials
| Part | Qty | Note |
|---|:---:|---|
| BTT SFS V2 |  1  | The Actual Product |
| M3x10 BHCS |  2  | BHCS Preferred but can use SHCS |
| M3x6 SHCS |  2  | Included in BTT Package |
| 30mm PTFE Tube |  2  | Included in BTT Package |
| M3 Nylock Nut |  2  | Can use Normal Nuts but Nylock will have less play |
| 5 pin JST-XH Connector |  1  | *** For SKR Mini E3 V3 *** |
| 2 pin JST-XH Connector |  1  | *** For SKR Pico *** |

## Printed Parts
First things first, we will need to take a few pins out from the existing connector. There are a number of depinning tools you can print out there. Some with mixed results....  
[JST XH Extractor by Gato](https://www.printables.com/model/353431-jst-xh-extractor)  
[JST-XH Depinner by GMagician](https://www.printables.com/model/480585-jst-xh-depinner)  
[JST-XH.2 Connector Depinner by Micro Center](https://www.printables.com/model/394200-jst-xh2-connector-depinner)    
[JST Connector Depinner by Rafa](https://www.printables.com/model/613127-jst-connector-depinner)  

And Of course you will want the [BTT SFS V2 Mount for Baby Belt Pro](/STLs/Mods/BTT%20SFS%20v2%20Mount.stl)

## Wiring
The Sensor Wire comes with the wires set up into two JST connectors. For the SKR Mini E3 V3 we will want to de-pin ALL the wires
in a "Pins Up / Wires left" view of the JST connector you will want the following order from Top to Bottom (As Seen here)

| Wire Color |
|------------|
| Green      |
| *EMPTY*    |
| Blue       |
| Red        |
| Black      |

SKR Mini E3 V3

This will plug into the Z-Probe Port on the board

SKR Mini E3 V3 Z Probe Port

For the SKR Pico you will use one of the existing connectors and because you have multiple places you *Could* put a ground there are different wire orders that are acceptable  

2 Pin Connector 

| Wire Order A  | Wire Order B |
|---|---|
| Blue | Blue |
| Black | **EMPTY** |

3 Pin Connector  

| Wire Order A  | Wire Order B |
|---|---|
| Green | Green |
| Red | Red |
| Black | **EMPTY** |

(No Picture Yet)

The 2 pin connector will plug into the PROBE port and the 3 pin connector to the SERVOS port on the SKR Pico

## Assembly

Step One is to grab your printed part and your choice of nuts, insert the nuts as seen here. (Nylock shown)  
Nuts Inserted into Mount  

Next, Grab the Sensor and the 2 M3x6 SHCS  
Place the Mount on the rear of the sensor with the text facing up as shown, and use the 2 M3x6 SHCS to connect the two pieces
You can attach your two PC4-M6 Pneumatic connectors from the package and screw them into both ends of the sensor unit as well  
Sensor Attached to Mount

Before you attach the sensor to the Baby Belt Pro "Tub", you will want to run the wire to your board and out through the square opening near the extruder    
Tub Mount Location

Check to ensure you can smoothly fit a M3 screw through both of the holes shown above, if not carefully ream them until it is easy to fit your M3 screw in. 

Take the Blue PTFE Tubes from the BTT Package and place them into both sides of the sensor, fitting the one loosely into the extruder as you place the sensor in place.  
You will then screw the 2 M3x10 screws from the inside of the tub into the printed mount. and it should look something like this.  

Tub Mount Location

## Config Changes
Once you have your wires in the correct setup for your board, You can grab our [options folder](/Software/Firmware/klipper/options) and add one or both of the following includes to your printer.cfg you will be good to go  
```aiignore
[include options/BTT_SFS_V2_MOTION.cfg] # Enable the motion sense feature of the BTT Smart filament Sensor V2
[include options/BTT_SFS_V2_SWITCH.cfg] # Enable the filament loaded feature of the BTT Smart filament Sensor V2
```

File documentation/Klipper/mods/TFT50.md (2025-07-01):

# Installing a PITFT50 on a BabyBelt Pro

Table o' Contents
- [BOM Differences](#bom-differences)
- [Printed Part Changes](#printed-part-changes)
- [Screen Changes](#screen-changes)
- [Validation](#validation)

## BOM Differences
- Remove BTT-TFT35-E3-V3.0 screen
- Add BTT Pi TFT50 (Preferrably v2.1)
- Add 3x M3x5x4 Heat set inserts
- Add 3x M3x14 SHCS
- Add 1x (300mm) Pi TFT Cable (Prefer Adafruit as the cable backer is shorter) 
  - Stock has a 5mm tall Backer, Amazon Special has 7mm Backer. You can trim this yourself if you are INCREDIBLY careful when both peeling up from the back and cutting, I take no responsibility if you damage your cable by modification.
- For the new X Belt Clamp (if the original BOM has not been updated)
  - 4 M3x10 (You can use whatever cap you like, I think BHCS looks best) * These are for the X Axis Belt Clamps
  - 4 M3x20 SHCS (These are to adjust your tension on both sides & to act as a pivot arm)
  - 6 M3 Normal Nuts

## Printed Part Changes
There are a few key differences in the assembly of the Baby Belt Pro for Klipper, the main differences are the front screen mount and a sensor switch. 

[Front Screen](../../../STLs/Mods/Klipper%20PiTFT50%20Screen/Klipper%20Screen%20Mount.stl)  
[Screen Cartridge](../../../STLs/Mods/Klipper%20PiTFT50%20Screen/Screen%20Cartridge%20-%20BTT%20PI%20TFT50%20v2%20cover.stl)

## Screen Changes
Now we get to the fun part! First thing's first, take your [Screen Cartridge](../../../STLs/Mods/Klipper%20PiTFT50%20Screen/Screen%20Cartridge%20-%20BTT%20PI%20TFT50%20v2%20cover.stl) and set your heatset inserts into both sides, making sure to put them in as straight as possible.   
Next we grab your BTT Pi TFT50 v2.1 (If you have wheels instead of buttons it should still fit, but this was all tested/validated on a 2.1 with just buttons) and the TFT Cable. insert one end into the screen with the pins facing up and then ensure it is locked in place with the lever down.  
Then set your screen into the cartridge case cable side first, it is going to fold it a little and that's fine. Once you have the cable side set in, pull the excess of the cable through the opening in the back and gently set the other side down. It should fit fairly flush with 0 force (see below)  
BTT PiTFT in Cartridge  

Now we want to set it down on the screen so we can secure it to the cartridge. If you have the screws that came with it those are great! If you are like me and lost them... well I have good news! An M2.5 x6 BHCS will do the job just as good!
2.5mm x6mm BHCS

Pick a Corner to start with, then go diagonally across, up and then diagonally back down (see picture)  
Screen Cartridge Screw Order  

Congrats! You've got a Screen Cartridge! If this were some other guide we'd tell you to eat a piece of candy.   

Moving on, we need to slot our screen cartridge into the housing, this can be a bit tricky but if you are careful it will be just fine.  
We want to take the cable that is currently connected inside our "screen cartridge" and feel it into the bottom slot of the screen holder.  
Feed the cable into the mount

Next tuck it around the back of the screen and carefully hold it with a finger while you start inserting the screen cartridge into the holder. 
Hold the Cable, Insert Cartridge  

Once you have inserted past the flex cable section of the screen you can let go of the cable and insert the screen the rest of the way in. Your cable should be towards the back of the housing and you should have access to the buttons from the cutout in the cartridge as seen here  
Check Your Work Inserting the Cartrige  

Next you will want to screw in the side Screws (M3x14 SHCS Qty: 3) start with the side with a single hole and just get it started without screwing all the way in.  
Then insert the upper screw on the other side and get it started, finally the bottom screw on that same side. If everything lines up, tighten all three screws down.  
If they do not all insert, see if you have to push the cartridge ever so slightly to get it to line up, if not check that you inserted the cartridge correctly and that all of your heat sets are as straight as possible.

Finally, Insert the other end of the flex cable into the raspberry pi's display port, pull up on the tab without removing it, and insert the cable We want to ensure we are giving the pins the raspberry and then push the tab back down to lock the cable in place.  
Give those Pins the Raspberry!

## Validation
Fire up the machine and ensure everything works!

Firstly the screen should turn on immediately, and you should see the Pi booting up!   
If it is upside down, press the middle button on the bottom of the Pi TFT50 to rotate it.

If you see the Pi Booting up, but it stays at a terminal you need to install KlipperScreen. I suggest installing it via [KIAUH](https://github.com/dw-0/kiauh)

If you can see the interface, but touch is not working AT ALL you will need to modify your /boot/config.txt
```bash
sudo nano /boot/config.txt
```

and change the line that has   
```bash
dtoverlay=vc4-kms-v3d
```  
to  
```bash
dtoverlay=vc4-fkms-v3d
```  

If you have any other problems, open an issue here on GitHub or reach out on the Baby Belt Discord.

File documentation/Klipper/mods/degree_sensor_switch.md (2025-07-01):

Table o' Contents
- [BOM Differences](#bom-differences)
- [Degree Sensor Switch Wiring](#degree-sensor-switch)
- [Installing the Switch](#installing-the-switch)
- [Config Changes](#printercfg-changes)
- [Validation](#validation)

## BOM Differences
- Add 1 Omron D2F-5L (or similar)
- Add 2x M2x10 Self Tapping Screws
- Approximately 160mm of 22-30AWG stranded wire
- JST-XH Female Crimp ends (SXH-001T-P0.6 or SXH-001T-P0.6N)
- JST-XH 3-wire housing (XHP-3)

## Degree Sensor Switch
Take the 22-30AWG wire and strip a small portion of it, solder a wire to each of the outer legs of the switch as seen here.  
After you have connected them, add your crimp ends then gently twist the two wires to keep things nice and tidy. When you have reached the end of the wires, grab the JST 3 pin Wire housing and insert them in the right two spots if viewing the connector in a "pins up" orientation [see here](#xhp-3-wiring).   
Switch Wiring Image

## XHP-3 wiring

XHP-3 image

## Installing the switch
Next, on [Side A](../../../../STLs/Frame/BBProV25fl_Side-A.stl) if you are using an existing part, take the D2F-5L switch and place it so that the face of the plastic is aligned with the front face of the case and the protruding side of the lever is closer to you.

Front View  
Front View  
Outside View  
Outside View  
Inside View  
Inside View

Next take the other end of the wire, now crimped and in it's housing and plug it into the main board.  
We will be using the E0-STOP port highlighted here in green.  
SKR mini E3 V3 wiring diagram

## printer.cfg changes
```jinja
[gcode_button 45_deg_check]
pin: PC15 #This is the setting for the SKR E3 Mini V3 using the E0STOP
press_gcode: SET_GCODE_VARIABLE MACRO=Y_ANGLE VARIABLE=state VALUE="45"
release_gcode: SET_GCODE_VARIABLE MACRO=Y_ANGLE VARIABLE=state VALUE="30"
```

## macros.cfg changes
You could also put these in your printer.cfg if you do not have macros.cfg broken out
```jinja
[gcode_macro PRINT_START]
# Reference https://github.com/KevinOConnor/klipper/blob/master/docs/Config_Reference.md#gcode_macroA
# On how to override default parameters
#default_parameter_BED_TEMP: 60
#default_parameter_EXTRUDER_TEMP: 200

gcode:
    {% set BED = params.BED|int %}
    {% set EXTRUDER = params.EXTRUDER|int %}
    {% set MATERIAL = params.MATERIAL|string %}
    {% set ANGLE = params.ANGLE|string %}
    {% set y_angle_state = printer["gcode_macro Y_ANGLE"].state|string %}

    #Uncomment the line below if you need to see the values and troubleshoot
    #RESPOND PREFIX="Debug - Y_angle_state: '{y_angle_state}' requested: '{ANGLE}'"
    
    {% if y_angle_state == ANGLE %}
        RESPOND PREFIX="Angle Verified... Continuing to Print!"

        G90 ; use absolute coordinates
        M83 ; extruder relative mode
        G28 ; home all axis

        M104 S150                      ; preheat nozzle to 150C
        M117 Heating Bed
        M190 S{BED}                    ; heat bed
    
        #Probe Everytime
	    #G29 
	    #load saved mesh at print start instead of probe. Uncomment to use but comment out G29
	    #BED_MESH_PROFILE LOAD=default
    
        M117 Heating Nozzle
        M109 S{EXTRUDER}               ; heat nozzle
        M190 S{BED}                    ; confirm bed temperature
        M117 ;Clear the message?
    
        # Move the nozzle near the bed
        G1 X0 Y0 Z5 F3000
        PRIME_RIGHT
        G0 Z5 F3000
        G21 ; set units to millimeters
        G90 ; use absolute coordinates
        M83 ; use relative distances for extrusion
        G92 E0
        
    {% else %}
        RESPOND PREFIX="Your Angle is set to {y_angle_state}, but you sliced for {ANGLE}"
        CANCEL_PRINT
    {% endif %}    

    [gcode_macro Y_ANGLE]
    variable_state: "30"
    gcode:
        RESPOND PREFIX="Y Angle is: {state}"
```

## Validation
Validation is simple, keep your X axis assembly off, power up the printer. Press the button and look at the console.  
It should read
```aiignore
Y Angle is: 45
```

When you let go it should read
```aiignore
Y Angle is: 30
```

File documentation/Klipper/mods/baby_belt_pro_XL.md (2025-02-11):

Love the BabyBelt Pro, but wish it was not so Baby? Try the BabyBelt Pro XL Mod to bring XL to your belt printing.  Make the X and Y axies 100mm (Or more) bigger!

From the mind of Rob Mink comes the GO BIG mod to the Baby Belt Pro, This mod is a Work in Progress and is subject to change. 

Table o' Contents
- [BOM](#bill-of-materials)
- [Thanks & Support](#thanks--support)

## Bill of Materials
| Part | Qty | Alt part | Note |
|---|---|---|---|
| Bamboo hot end | 1 | E3D Micro W. Non Planer Nipple Noz 24v, note need a 3010 fan then | |
| Nema 11 stepper motor - 1.8 degree 10Ncm 28X28X45 recc - for X/Y | 2 | Most bipolar (4 wire) Nema 11s will work here | |
| Nema 17 stepper motor - 1.8 degree 55Ncm recc - For Z/E | 2 | Most bipolar (4 wire) Nema 17s will work here | |
| 30MM by 10MM blower Fan 24V -parts cooling | 1 | | |
|  25 MM  Fan (for Bamboo hotend) 24v | 1 | 3010 brushless fan 24V (for E3d hotend) | |
| Power jack | 1 | | |
| Power switch | 1 | | |
| SKR Mini E3V3 | 1 | | |
| BTT-TFT35-E3-V3.0 screen | 1 | CR-10 Style Screen | |
| GT2 Belt | Under 2.5 M | | |
| M8 Bolt 70MM | 6 | | |
| M8 Nut | 8 | | |
| 608 Bearing | 4 | | |
| MGN7H 250MM Linear rail | 1 | | |
| MGN12C 250MM Linear Rail | 1 | | |
| GT2 Idler 16 T (SMOOTH, no teeth)  3MM bore | 3 | | |
| GT2 Pully 16T 5MM Bore | 2 | | |
| M3 bolts 10MM | 30 | | |
| M3 bolts 20MM | 35 | | |
| M3 Heatset nuts | 10+ | | |
| M3 Nuts | 32 | | |
| M2 Bolts 6MM | 12 | | |
| M2 nuts | 8 | | |
| M2.5 Bolts 8 MM | 8 | | For Nema 11 |
| M2.5 bolts 12 MM (For Bambu Hotend) | 2 | | Holds 25MM fan to bottom of hotend for Bambu |
| M2.5 washer | 8 | | Not 100 needed, but recc, More reinforcment for Nema 11 |
| Extruder that bolts to Nema17 | 1 | | Any normal extruder that uses a nema 17 motor, EG e3d Titan or Bondtech BMG |
| PTFE Tube for extruder | 850 MM ? | Capricon tube - need to check | |
| Collet holder for PTFE (Bambu ONLY) | 1 | | |
| Zipties for wires | 25 | | |
| Print belt | 1 | VIDEO is not for a PRO. | Use google doc Measure accordingly (15in long & 5 in Wide!) |
| Underbed WIP | 1 | or go unheated | |
| 24V 6 A barrel power supply  (8 amps if using a heated bed) | 1 | | |

## Thanks & Support
Please Consider Donating to Marlin [Donate to Marlin](https://marlinfw.org/docs/development/contributing.html)  
Or Klipper [Donate to Klipper](https://www.klipper3d.org/Sponsors.html)  
Or Me? [Printcepts Patreon](https://www.patreon.com/Printcepts)

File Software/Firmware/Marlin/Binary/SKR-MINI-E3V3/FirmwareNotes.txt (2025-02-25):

Motor current for X and Y may be high, depends on motors, try around 380mA

You need to set the steps for your extruder!

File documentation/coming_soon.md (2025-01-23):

<p align="center">
  Coming Soon
</p>

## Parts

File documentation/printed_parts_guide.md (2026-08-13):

# BabyBelt Pro V2 Printed Parts List
BabyBelt Pro V2 by RobMink

## Introduction
Hello! This is the printed parts guide for the BabyBelt Pro V2 by RobMink. 

How to read this guide:
 - Printed Parts will link to the specific file in the GitHub if clicked on
 - Printed part name prefixes include
   - [a] = accent color
   - [s] = needs supports
   - [i] = needs heat-set inserts
   - [HT] = should be printed in a strong heat tolerant material (PETG, ABS, ASA, PA) to avoid premature wearing

## Printed Parts
### Printing Parts
Most of the parts of this kit can be printed out of normal PLA, allowing for a wide range of colors and stylistic choices! The parts that shouldn't be printed out of PLA are listed below. A good rule of thumb is if you only ever plan to print PLA or TPU, your Bed/Underbed can be PETG. However, if printing in PETG, it is **HIGHLY** suggested to use ABS or ASA. 

- [*NEMA17_ZGear*](../STLs/ZBeltDrive/[a]_BBProV25fl_Nema17_ZGear.stl)
- [*Roller_ZGear*](../STLs/ZBeltDrive/[a]_BBProV25fl_Roller_ZGear.stl)
- [*UnderbedOrBed*](../STLs/ZBeltDrive/[HT]_BBProV25fl_UnderbedOrBed.stl)

We recommend printing all parts with standard Voron style settings:

- Layer height: 0.2mm
- Extrusion width: 0.4mm, forced
- Infill percentage: 40%
- Infill type: grid, gyroid, honeycomb, triangle, or cubic
- Wall count: 4, use 5 walls on [[a,s]_BBProV25fl_Roller[x2]](../STLs/ZBeltDrive/[a,s]_BBProV25fl_Roller[x2].stl)
- Solid top/bottom layers: 5

## Part List
|Name|Image|Area|Color|Supports|Heat-Sets|Material|Description
|-----|-----|-----|-----|-----|-----|-----|-----
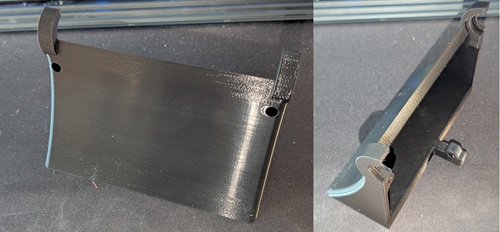
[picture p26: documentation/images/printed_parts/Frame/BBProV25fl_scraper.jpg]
BBProV25fl_scraper
|[BBProV25fl_scraper](../STLs/Frame/BBProV25fl_scraper.stl)||Frame|Main|No|No|>= PLA|
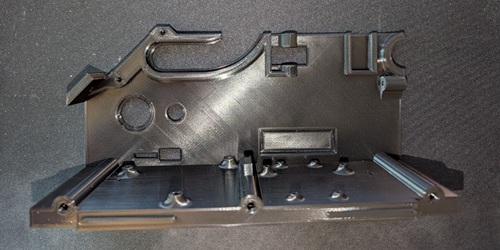
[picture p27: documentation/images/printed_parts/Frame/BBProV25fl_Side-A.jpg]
BBProV25fl_Side-A
|[BBProV25fl_Side-A](../STLs/Frame/BBProV25fl_Side-A.stl)||Frame|Main|No|No|>= PLA|
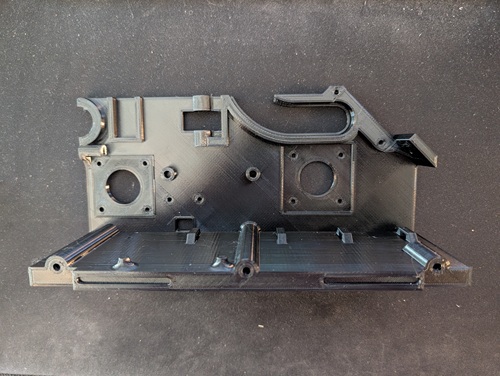
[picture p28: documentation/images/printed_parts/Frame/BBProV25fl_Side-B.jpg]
BBProV25fl_Side-B
|[BBProV25fl_Side-B](../STLs/Frame/BBProV25fl_Side-B.stl)||Frame|Main|No|No|>= PLA|
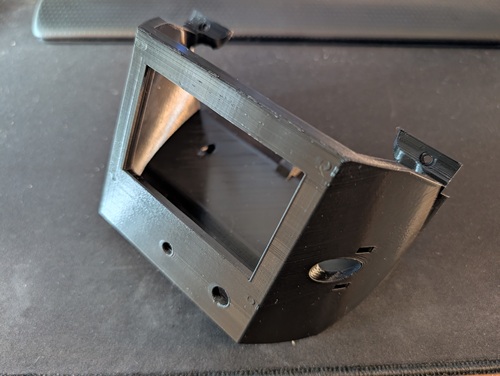
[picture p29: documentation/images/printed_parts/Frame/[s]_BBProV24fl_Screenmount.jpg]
[s]_BBProV24fl_Screenmount
|[[s]_BBProV24fl_Screenmount](../STLs/Frame/[s]_BBProV24fl_Screenmount.stl)||Frame|Main|Yes|No|>= PLA|
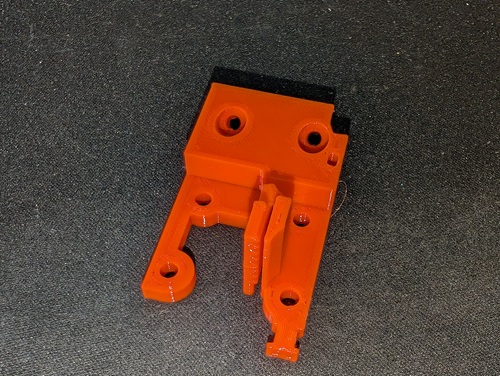
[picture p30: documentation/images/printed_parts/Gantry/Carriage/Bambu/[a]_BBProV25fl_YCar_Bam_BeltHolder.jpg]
[a]_BBProV25fl_YCar_Bam_BeltHolder
|[[a]_BBProV25fl_YCar_Bam_BeltHolder](../STLs/Gantry/Carriage/Bambu/[a]_BBProV25fl_YCar_Bam_BeltHolder.stl)||Gantry/Carriage/Bambu|Accent|No|No|>= PLA|
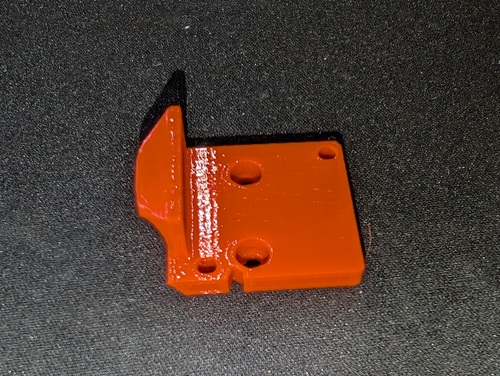
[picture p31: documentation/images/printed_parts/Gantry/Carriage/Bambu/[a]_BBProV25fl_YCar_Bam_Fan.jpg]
[a]_BBProV25fl_YCar_Bam_Fan
|[[a]_BBProV25fl_YCar_Bam_Fan](../STLs/Gantry/Carriage/Bambu/[a]_BBProV25fl_YCar_Bam_Fan.stl)||Gantry/Carriage/Bambu|Accent|No|No|>= PLA|
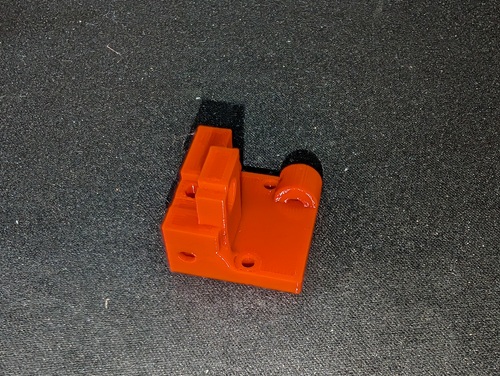
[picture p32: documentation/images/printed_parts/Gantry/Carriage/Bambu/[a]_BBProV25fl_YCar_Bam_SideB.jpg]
[a]_BBProV25fl_YCar_Bam_SideB
|[[a]_BBProV25fl_YCar_Bam_SideB](../STLs/Gantry/Carriage/Bambu/[a]_BBProV25fl_YCar_Bam_SideB.stl)||Gantry/Carriage/Bambu|Accent|No|No|>= PLA|
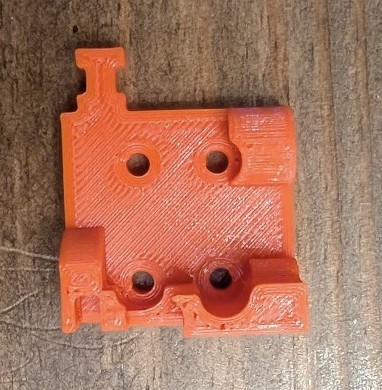
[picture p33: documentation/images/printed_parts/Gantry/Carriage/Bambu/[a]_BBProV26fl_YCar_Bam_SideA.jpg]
[a]_BBProV26fl_YCar_Bam_SideA
|[[a]_BBProV26fl_YCar_Bam_SideA](../STLs/Gantry/Carriage/Bambu/[a]_BBProV26fl_YCar_Bam_SideA.stl)||Gantry/Carriage/Bambu|Accent|No|No|>= PLA|
|[[i]_BBProV26fl_X-Carraige](../STLs/Gantry/X/[i]_BBProV26fl_X-Carraige.stl)|[i]_BBProV26fl_X-Carraige|Gantry/X|Main|No|Yes|>= PLA|
|[BBProV26fl_X-CarraigeMotorMount](../STLs/Gantry/X/BBProV26fl_X-CarraigeMotorMount.stl)|BBProV26fl_X-CarraigeMotorMount|Gantry/X|Main|No|No|>= PLA|
|[[a]_BBProV25fl_pivotArm(2x)](../STLs/Gantry/X/[a]_BBProV25fl_pivotArm(2x).stl)|[a]_BBProV25fl_pivotArm(2x)|Gantry/X|Accent|No|No|>= PLA|
|[[a]_BBProV25fl_XPivotClamp(2x)](../STLs/Gantry/X/[a]_BBProV25fl_XPivotClamp(2x).stl)|[a]_BBProV25fl_XPivotClamp(2x)|Gantry/X|Accent|No|No|>= PLA|
|[[a]_BBProV26fl_XrailMount-SideA](../STLs/Gantry/X/[a]_BBProV26fl_XrailMount-SideA.stl)|[a]_BBProV26fl_XrailMount-SideA|Gantry/X|Accent|No|No|>= PLA|
|[[a]_BBProV26fl_XrailMount-SideB](../STLs/Gantry/X/[a]_BBProV26fl_XrailMount-SideB.stl)|[a]_BBProV26fl_XrailMount-SideB|Gantry/X|Accent|No|No|>= PLA|
|[[ai]_BBProV26fl_XrailMountUnder-SideA](../STLs/Gantry/X/[ai]_BBProV26fl_XrailMountUnder-SideA.stl)|[ai]_BBProV26fl_XrailMountUnder-SideA|Gantry/X|Accent|No|Yes|>= PLA|
|[[ai]_BBProV26fl_XrailMountUnder-SideB](../STLs/Gantry/X/[ai]_BBProV26fl_XrailMountUnder-SideB.stl)|[ai]_BBProV26fl_XrailMountUnder-SideB|Gantry/X|Accent|No|Yes|>= PLA|
|[BBProV25fl_RockMonsterNo1YTentionerNut](../STLs/Gantry/Y/BBProV25fl_RockMonsterNo1YTentionerNut.stl)|BBProV25fl_RockMonsterNo1YTentionerNut|Gantry/Y|Main|No|No|>= PLA|
|[BBProV26fl_LinearRailReplacement](../STLs/Gantry/Y/BBProV26fl_LinearRailReplacement.stl)|BBProV26fl_LinearRailReplacement|Gantry/Y|Main|No|No|>= PLA|
|[LDO Kit - Toolboard Mount v1](../STLs/Gantry/Y/LDO%20Kit%20-%20Toolboard%20Mount%20v1.stl)|LDO Kit - Toolboard Mount v1|Gantry/Y|Main|No|No|>= PLA|
|[[a]_BBProV25fl_RockMonsterNo1YTentionerIdlerHolder](../STLs/Gantry/Y/[a]_BBProV25fl_RockMonsterNo1YTentionerIdlerHolder.stl)|[a]_BBProV25fl_RockMonsterNo1YTentionerIdlerHolder|Gantry/Y|Accent|No|No|>= PLA|
|[[a]_BBProV26fl_RockMonsterNo1YTentionerBody](../STLs/Gantry/Y/[a]_BBProV26fl_RockMonsterNo1YTentionerBody.stl)|[a]_BBProV26fl_RockMonsterNo1YTentionerBody|Gantry/Y|Accent|No|No|>= PLA|
|[[a]_BBProV25fl_PrintBelt-Frame-A](../STLs/PrintBelt/[a]_BBProV25fl_PrintBelt-Frame-A.stl)|[a]_BBProV25fl_PrintBelt-Frame-A|PrintBelt|Accent|No|No|>= PLA|
|[[a]_BBProV25fl_PrintBelt-Frame-B](../STLs/PrintBelt/[a]_BBProV25fl_PrintBelt-Frame-B.stl)|[a]_BBProV25fl_PrintBelt-Frame-B|PrintBelt|Accent|No|No|>= PLA|
|[[a]_BBProV25fl_PrintBelt-Nut(2x)](../STLs/PrintBelt/[a]_BBProV25fl_PrintBelt-Nut(2x).stl)|[a]_BBProV25fl_PrintBelt-Nut(2x)|PrintBelt|Accent|No|No|>= PLA|
|[[a]_BBProV25fl_PrintBelt-Pusher-A](../STLs/PrintBelt/[a]_BBProV25fl_PrintBelt-Pusher-A.stl)|[a]_BBProV25fl_PrintBelt-Pusher-A|PrintBelt|Accent|No|No|>= PLA|
|[[a]_BBProV25fl_PrintBelt-Pusher-B](../STLs/PrintBelt/[a]_BBProV25fl_PrintBelt-Pusher-B.stl)|[a]_BBProV25fl_PrintBelt-Pusher-B|PrintBelt|Accent|No|No|>= PLA|
|[[a,s]_BBProV25fl_Roller[x2]](../STLs/ZBeltDrive/[a,s]_BBProV25fl_Roller[x2].stl)|[a,s]_BBProV25fl_Roller[x2]|ZBeltDrive|Accent|Yes|No|>= PLA|
|[[a]_BBProV25fl_Nema17_ZGear](../STLs/ZBeltDrive/[a]_BBProV25fl_Nema17_ZGear.stl)|[a]_BBProV25fl_Nema17_ZGear|ZBeltDrive|Accent|No|No|>= PETG|
|[[a]_BBProV25fl_Roller_ZGear](../STLs/ZBeltDrive/[a]_BBProV25fl_Roller_ZGear.stl)|[a]_BBProV25fl_Roller_ZGear|ZBeltDrive|Accent|No|No|>= PETG|
|[[HT]_BBProV25fl_Underbed-notforbed-FOR_LDO_HEATBED](../STLs/ZBeltDrive/[HT]_BBProV25fl_Underbed-notforbed-FOR_LDO_HEATBED.stl)|[HT]_BBProV25fl_Underbed-notforbed-FOR_LDO_HEATBED|ZBeltDrive|Main|No|No|>= PETG| Use this when installing LDO bed heater.
|[[HT]_BBProV25fl_UnderbedOrBed](../STLs/ZBeltDrive/[HT]_BBProV25fl_UnderbedOrBed.stl)|[HT]_BBProV25fl_UnderbedOrBed|ZBeltDrive|Main|No|No|>= PETG| Use this for no heated bed.

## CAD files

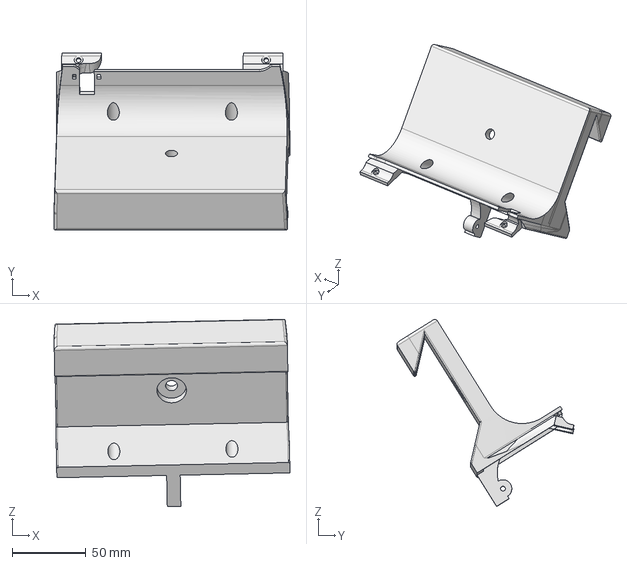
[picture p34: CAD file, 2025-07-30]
CAD/frenchCleatMount.stp
159.9 x 119.7 x 126.8 mm

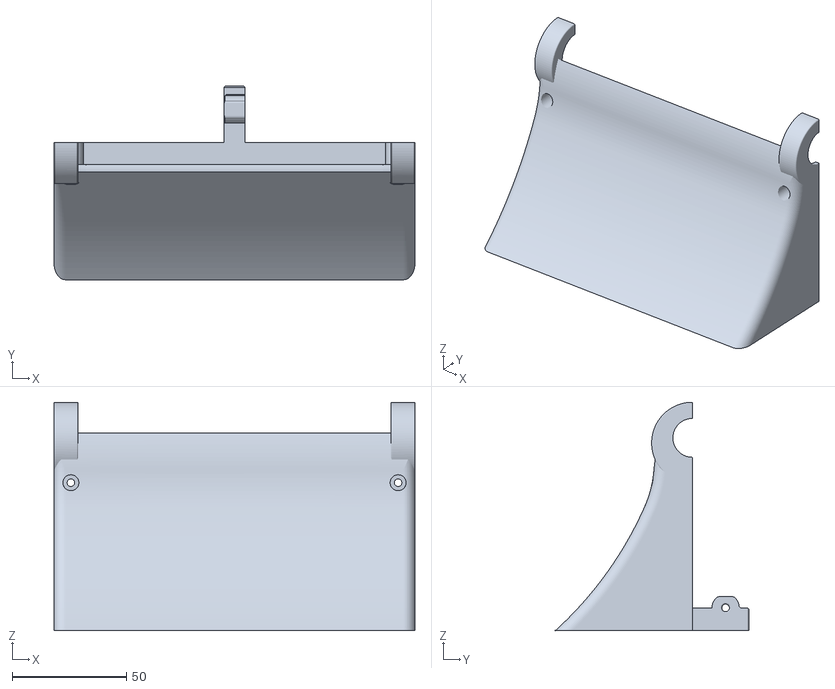
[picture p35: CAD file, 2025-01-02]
STLs/Frame/BBProV25fl_scraper.stl
158.0 x 84.7 x 100.0

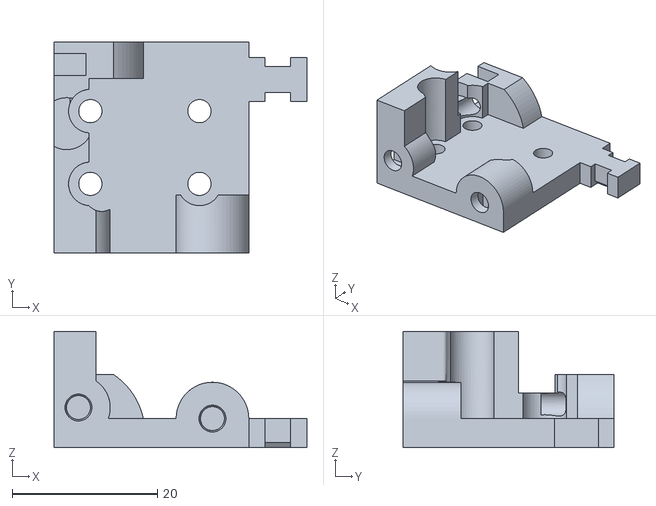
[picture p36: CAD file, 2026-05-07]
STLs/Gantry/Carriage/Bambu/[a]_BBProV26fl_YCar_Bam_SideA.stl
34.8 x 29.0 x 16.0

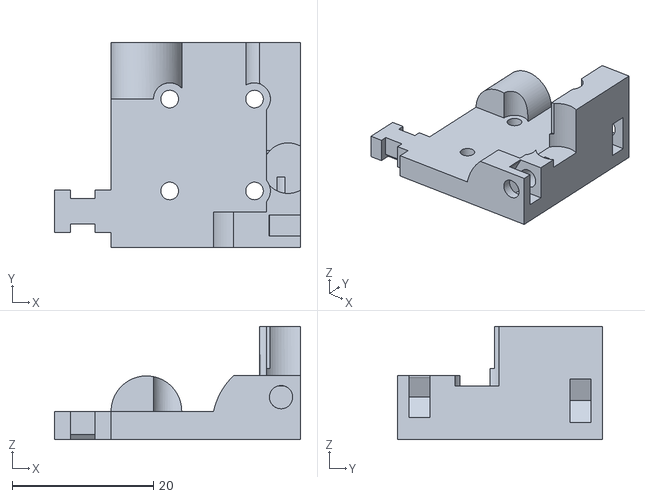
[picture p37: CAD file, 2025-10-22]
STLs/Gantry/Carriage/Bambu/ECAS version/[a]_BBProV25fl_YCar_Bam_SideA_ECAS.stl
34.8 x 29.0 x 16.0

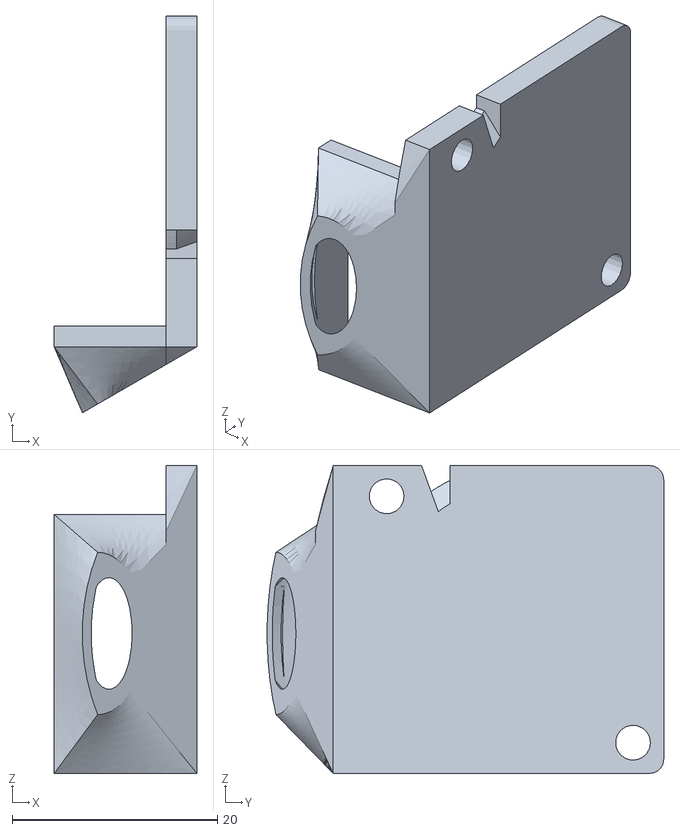
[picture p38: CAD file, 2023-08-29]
STLs/Gantry/Carriage/Revo - TODO Update for 2.6- DO NOT USE/[a]_BBPro_partsfanmount.stl
13.9 x 38.6 x 30.0

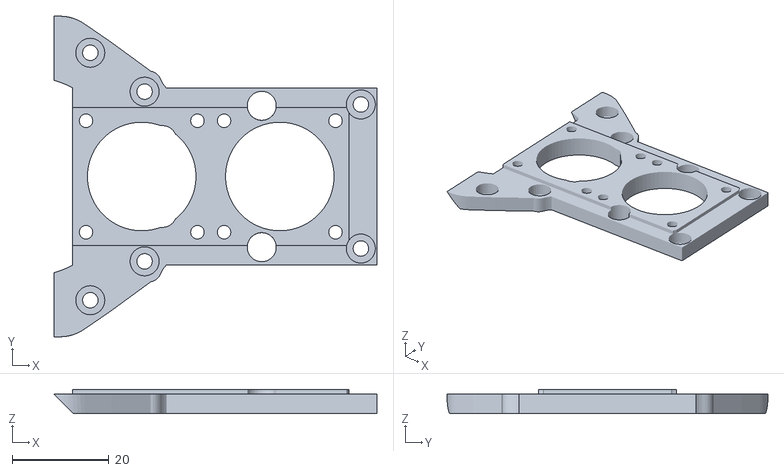
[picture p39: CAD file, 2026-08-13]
STLs/Gantry/X/BBProV26fl_X-CarraigeMotorMount.stl
66.7 x 66.2 x 5.00

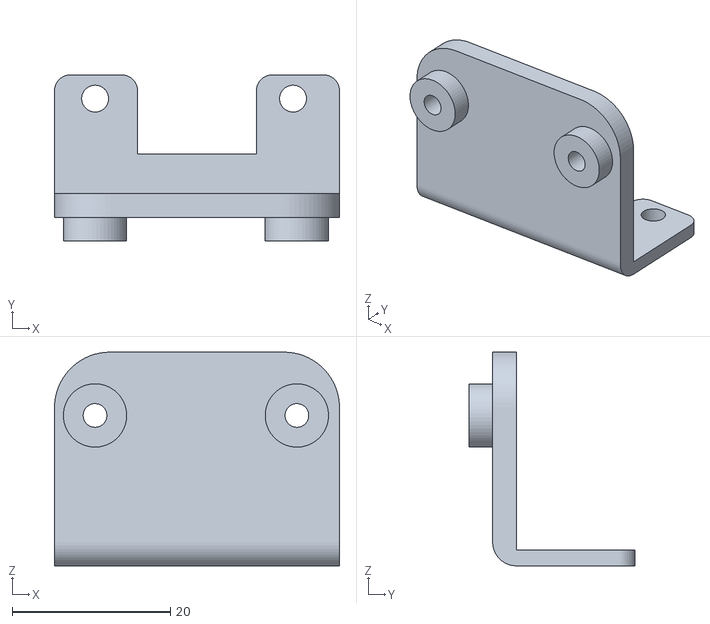
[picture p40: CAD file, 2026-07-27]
STLs/Gantry/Y/LDO Kit - Toolboard Mount v1.stl
36.0 x 21.0 x 27.0

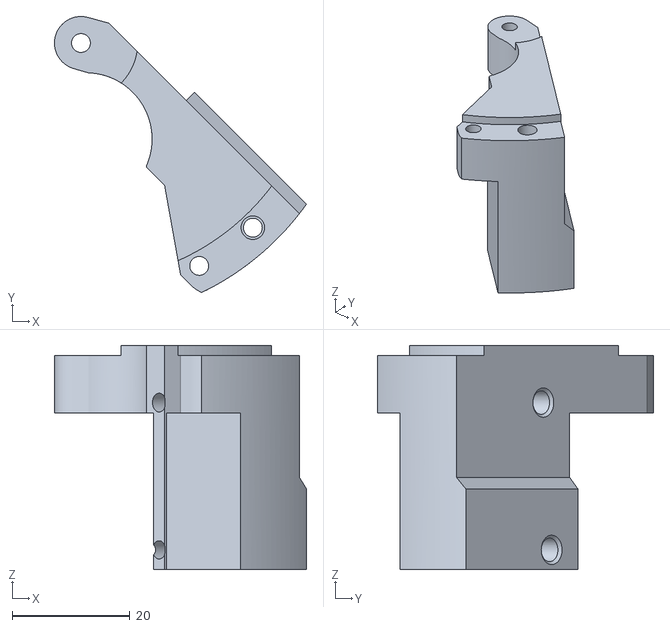
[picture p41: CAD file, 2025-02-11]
STLs/Mods/Baby Belt Pro XL - WIP/XLMod_under-mgn12mod-powerside_NeedsHeatset.stl
42.8 x 46.8 x 38.1

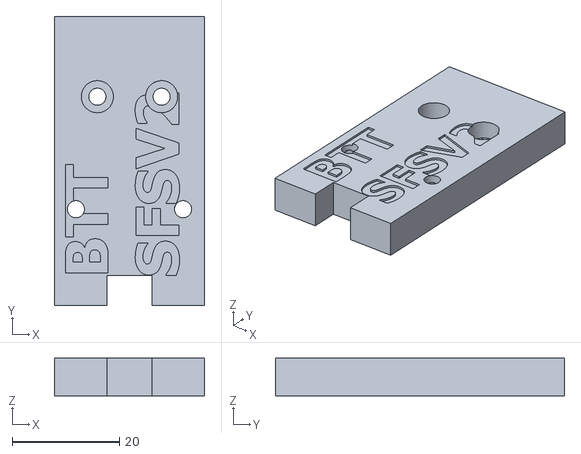
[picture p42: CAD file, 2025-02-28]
STLs/Mods/BTT SFS v2 Mount.stl
28.0 x 54.0 x 7.00

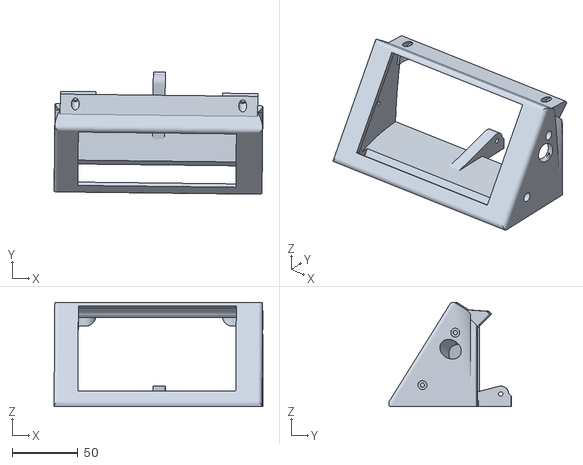
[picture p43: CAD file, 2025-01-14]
STLs/Mods/Klipper PiTFT50 Screen/Klipper Screen Mount.stl
158.7 x 93.0 x 79.4

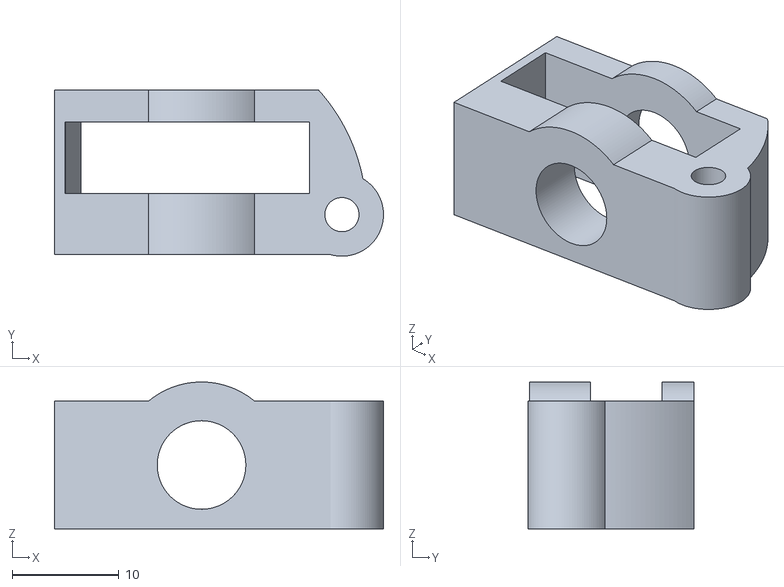
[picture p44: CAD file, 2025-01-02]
STLs/PrintBelt/[a]_BBProV25fl_PrintBelt-Frame-A.stl
30.8 x 15.6 x 13.8

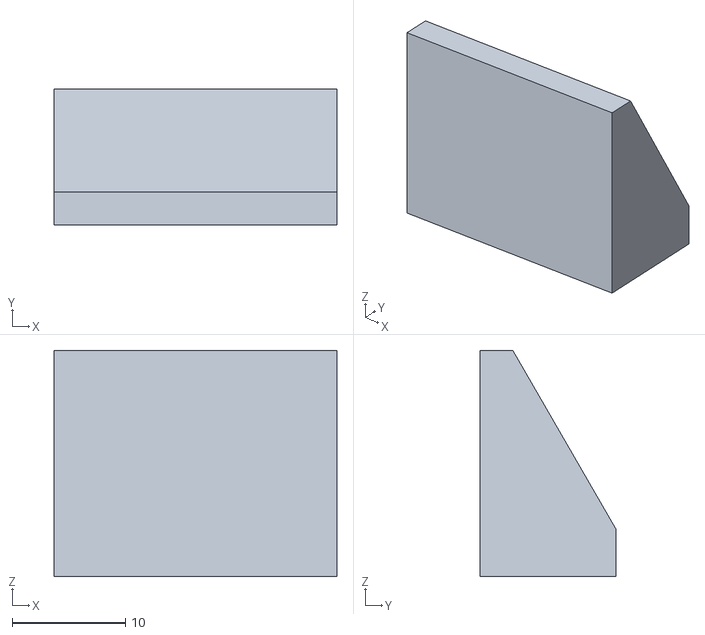
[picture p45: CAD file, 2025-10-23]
STLs/Tools/30deg EM Flow Test Block.stl
25.0 x 12.0 x 20.0

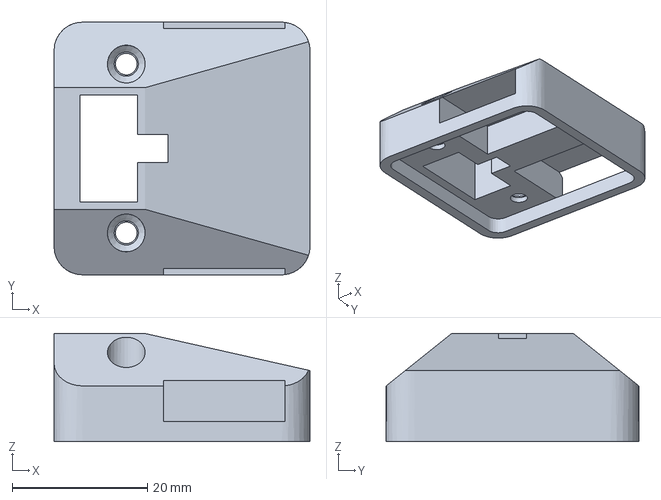
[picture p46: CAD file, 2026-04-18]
STLs/User Mods/kilotick/BBP extruder board cover angled v2.3mf
37.9 x 37.4 x 16.0 mm

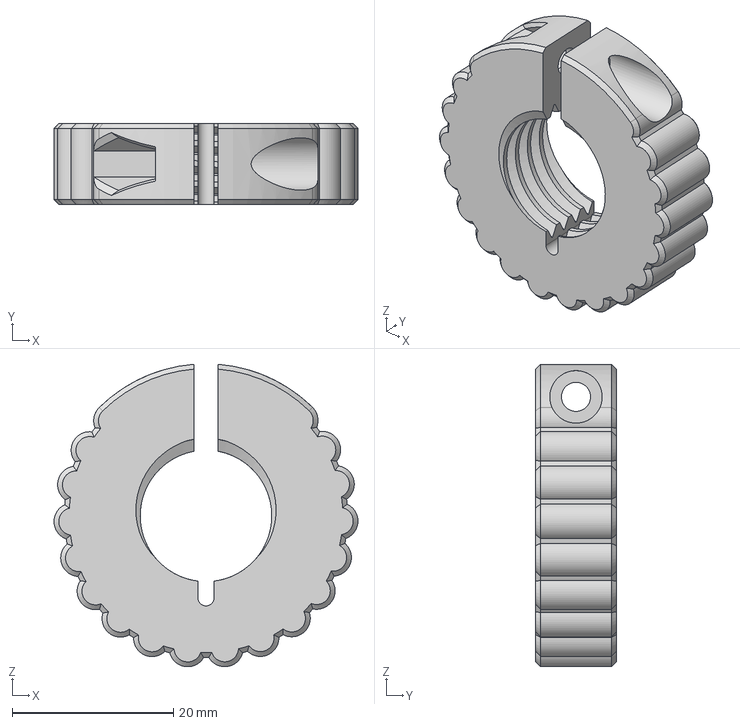
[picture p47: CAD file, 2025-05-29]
STLs/User Mods/Madeline/Locking Y Tensioner Nut/BBProV2_RockMonsterNo1YTentionerNut Locking.step
37.7 x 10.0 x 37.5 mm

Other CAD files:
STLs/ZBeltDrive/[HT]_BBProV25fl_Underbed-notforbed-FOR_LDO_HEATBED.stl
STLs/Frame/BBProV25fl_Side-B.stl
STLs/Gantry/Carriage/Bambu/[a]_BBProV25fl_YCar_Bam_Fan.stl
STLs/Gantry/Carriage/Bambu/ECAS version/[a]_BBProV25fl_YCar_Bam_SideB_ecas-Looser.stl
STLs/Frame/BBProV25fl_Side-A.stl
STLs/Frame/[s]_BBProV24fl_Screenmount.stl
STLs/Gantry/Carriage/Bambu/ECAS version/[a]_BBProV25fl_YCar_Bam_SideB_ecas-Tight.stl
STLs/Gantry/Carriage/Bambu/[a]_BBProV25fl_YCar_Bam_BeltHolder.stl
STLs/Gantry/Carriage/Bambu/[a]_BBProV25fl_YCar_Bam_SideB.stl
STLs/Gantry/Carriage/Revo - TODO Update for 2.6- DO NOT USE/[a]_BBPro_YCar-WireAndBelt_17.stl
STLs/Gantry/Carriage/Revo - TODO Update for 2.6- DO NOT USE/[a]_BBPro_YCarLside_A.stl
STLs/Gantry/Carriage/Revo - TODO Update for 2.6- DO NOT USE/[a]_BBPro_YCarLside_B.stl
STLs/Gantry/Carriage/Revo - TODO Update for 2.6- DO NOT USE/[a]_BBPro_fanduct.stl
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

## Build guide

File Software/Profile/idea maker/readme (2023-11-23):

This is the slicer I typicaly use.  Its hard to learn, but pretty powerful

download link here- https://www.raise3d.com/ideamaker/

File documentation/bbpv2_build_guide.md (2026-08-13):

  

# BabyBelt Pro V2.5 - Printer Buy and Build Guide
BabyBelt Pro V2.5 by RobMink

Jump To...

- [Pre-Purchase and Print Decisions](#pre-purchase-and-print-decisions)
- [Tools Needed](#Tools-Needed)
- [Printed and Made Parts](#Printed-and-Made-Parts)
- [Purchased Parts](#Purchased-Parts)
- [Physical Build](#Physical-Build)
    - [Frame](#frame)
        - [Base Assembly](#base-assembly)
        - [Board Prep and Mount](#board-prep-and-mount)
        - [Power Switch and Jack](#power-switch-and-jack)
        - [Screen Mount](#screen-mount)
        - [Extruder](#extruder)
        - [Belt Tensioner](#belt-tensioners)
        - [Rollers](#rollers)
        - [Z-Motor](#z-motor)
        - [Scraper Install](#scraper-install)
    - [Gantry](#Gantry)
        - [Heatset Install](#heatset-install)
        - [X Carriage](#X-Carriage)
        - [Y Carriage](#Y-Carriage)
            - [Bowden Connector](#bowden-connector)
        - [Hotend Electronics](#Hotend-Electronics)
        - [Heatbreak Fan](#Heatbreak-fan)
        - [Y Tensioner](#Y-Tensioner)
        - [Y Axis](#Y-Axis)
        - [Y Axis GT2 Belt](#y-axis-gt2-belt)
        - [Mount Steppers](#mount-steppers) 
        - [X Axis GT2 Belt](#x-axis-gt2-belt)
        - [LDO Toolboard](#ldo-toolboard)
        - [Gantry Completion](#gantry-completion)
    - [Heated Bed](#heated-bed)
        - [No Heated Bed](#no-heated-bed)
        - [LDO Kit Heated Bed](#ldo-kit-heated-bed)
        - [Fabreeko Kit Heated Bed](#fabreeko-kit-heated-bed)
    - [Wiring](#wiring)
    - [Belt and Bed](#belt-and-bed)
    - [Build Complete](#build-complete)

- [Complete](#Complete)

## Pre-Purchase and Print Decisions
There are a few decisions that have an impact on the parts that need purchased and printed.

1. Hotend Choice - Bambu X1 or Revo
    - A Bambu X1 style hotend is the "default" included in both commercial kits and is a cheaper solution.
        - To use a bambu X1 style hotend print the bambu carriage parts, purchase a X1 style hotend such as the [Triangle Lab TZ 2.0 for Bambu X1](https://trianglelab.net/products/tz-20-hotend-for-bambu-lab-x1-p1p?VariantsId=11766), and a 25mm 24v fan for parts cooling.  If buying a kit only the printed parts are needed outside of what is included.
    - A Revo hotend can also be used.  This is a more expensive hotend but some folks opt for this solution for ease of nozzle changes and the [Revo Belt & Non Planar Nozzles](http://e3d-online.com/products/revo-belt-nozzles).
        - To use a Revo hotend print the revo carriage parts, purchase a Revo Micro 24v full hotend kit, a revo belt & non-planar nozzle, and a 3010 brushless 24v fan for parts cooling.

1. Firmware - Marlin or Klipper
    - Marlin Firmware - can be run with the basic BOM or either commercial kits with no additional hardware outside of a Micro SD card.  The screen will be the primary interface, firmware and gcode files are moved to the printer using the SD card or something external like Octoprint.
 
    - Klipper firmware - is a bit more popular but does require additional hardware.  The Baby Belt Pro v2.5 is designed with mounts for a Raspberry Pi 3/4/5 or CM 3/4 and a mount for a 24v to 5v buck converter to keep the setup internal.
        - Raspberry Pi or other SBC
        - Second Micro SD card or other boot media for the SBC
        - Power source for the SBC
            - A second external PSU can be run into the tub or a [Buck converter](https://www.amazon.com/dp/B0CRVVWL4Y) can be spliced to the power jack and keep all the power inside the tub.
        - The USB cable included with the SKR Mini can be used to connect the Pi to the SKR or 3 [~20CM female to female jumper wires](https://www.amazon.com/dp/B0BRTJQGS6) can be used to make a serial/uart connection inside the tub.  Follow the [uart connection guide](./Klipper/mods/uart_connection.md) for more detail.

[Jump to Top](#top)

## Tools Needed
- 2.5mm Hex Key or Driver
- 2mm Hex Key or Driver
- 1.5mm Hex Key or Driver
- Small Flathead Screwdriver
- Adjustable Wrench
- Wire Cutters
- File, knife, and/or deburring tool (Good for making slight adjustments to plastic parts if needed.)
- Electrical tape - or any thin tape to go on the rollers to add friction

[Jump to Top](#top)

## Printed and Made Parts
- Fabric Belt - Included in LDO/Fabreeko kits OR follow the [Fabric Belt Guide](belt_guide.md) to make one.
- Printed Parts - Check out the [Printed Parts Guide](printed_parts_guide.md) for parts description and print settings.
    - NOTE: Print EITHER the Bambu (LDO/Fabreeko kits) OR the Revo carriage parts.
    - NOTE: [Printed Parts Guide](printed_parts_guide.md) assumes BOM parts. Mods like SFS of TFT50 will require some additional/replaced parts.

[Jump to Top](#top)

## Purchased Parts
### SD Card
- One MicroSD card is needed for the SKR board (klipper or marlin) and is not included on the BOM or in any kit. The SKR can only read FAT32 so anything larger than a 32gb card will not be usable.
- If using Klipper and booting a pi from microSD get a second card of any size.
### Klipper extras
If Klipper will be used, remember to purchase the necessary extra parts listed in the [Klipper Firmware](#klipper-firmware) decision.
### Ways to Purchase
There are 3 main paths to getting the purchased parts. Kits are the easiest option and come with all non-printed parts needed to build a functional Baby Belt Pro v2.5 running Marlin.  
1. Self Source - [BB Pro v2.5 BOM](https://docs.google.com/spreadsheets/d/19PbR3nFbQ4-eIOTU0kmoTl5-mHv_KsTnUdfFXekWg-I/edit)
2. LDO Systems and West3D Kit - [LDO Kit BOM](./images/ldo_kit/unboxing/bom.jpg) - Buy the LDO System Kit @ [West3D](https://west3d.com/products/baby-belt-pro-v2-5-complete-diy-belt-printer-kit-by-ldo-systems-and-west3d) - In Stock as of Dec 2025
3. Fabreeko and HoneyBadger Kit - [Fabreeko/HoneyBadger Kit](https://www.fabreeko.com/products/baby-belt-pro-kit-by-honeybadger) - Out of Stock as of Dec 2025

[Jump to Top](#top)

# Physical Build 
>[!TIP]
>There are several times during this build when a component will be secured with multiple screws. It is generally recommended to NOT fully tighten a screw before the rest have been started, to make sure parts line up correctly and don't crack. 
## Frame
### Base Assembly
Start by constructing the base. 
- Place an **M3 Nut** into the hole indicated by the arrow in [*Side-B*](../STLs/Frame/BBProV25fl_Side-B.stl)
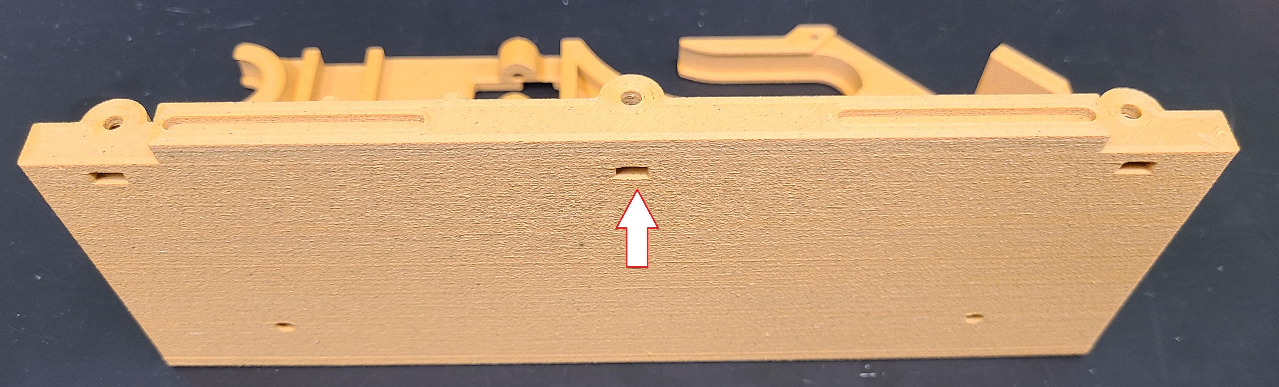
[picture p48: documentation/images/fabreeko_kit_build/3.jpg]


- Join the two sides together and place one **M3x20 screw** into the indicated hole in [*Side-A*](../STLs/Frame/BBProV25fl_Side-A.stl) and tighten. 
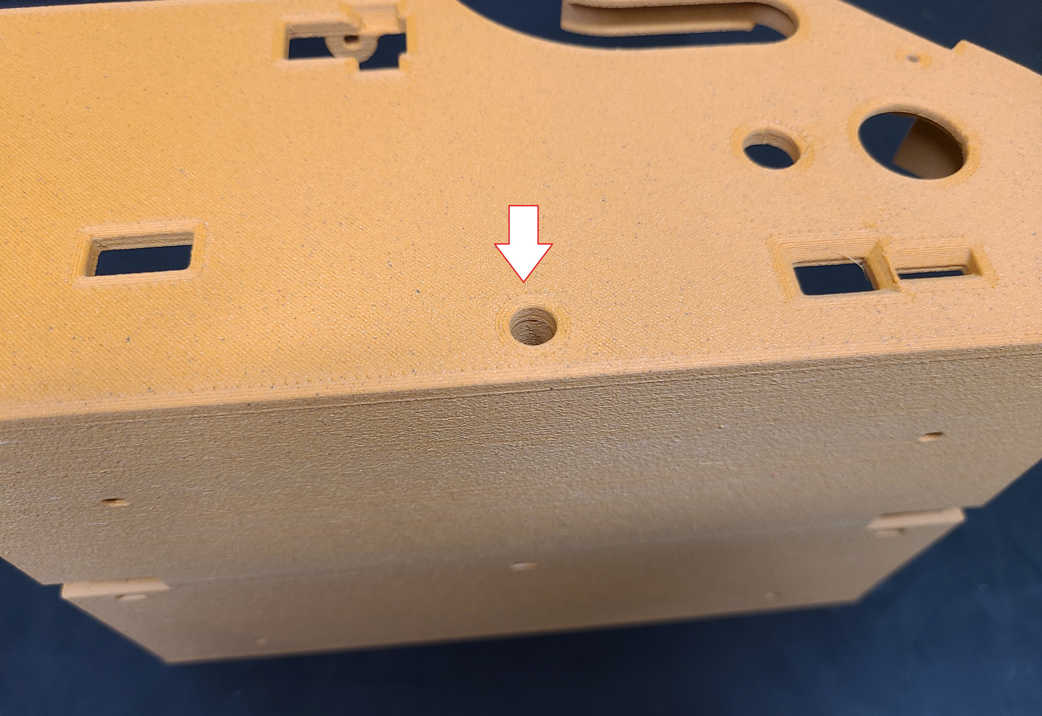
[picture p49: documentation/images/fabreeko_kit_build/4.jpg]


The base should now look like this.

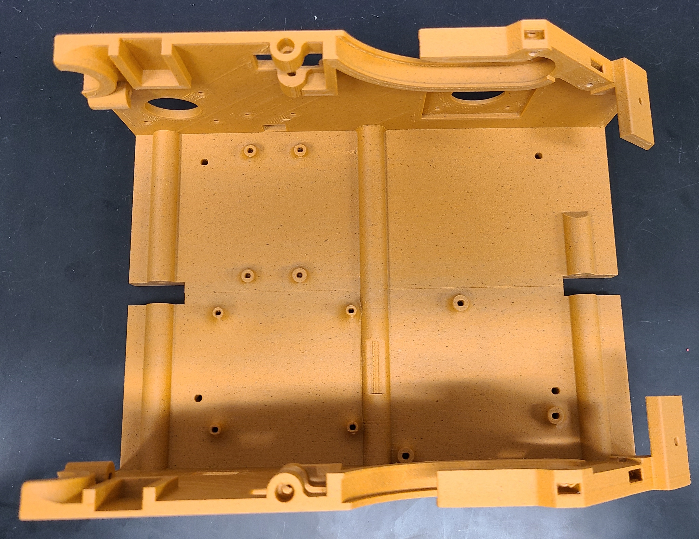
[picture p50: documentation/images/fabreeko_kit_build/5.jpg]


[Jump to Top](#top)

### Board Prep and Mount

- Unpack the board and locate the included jumpers.

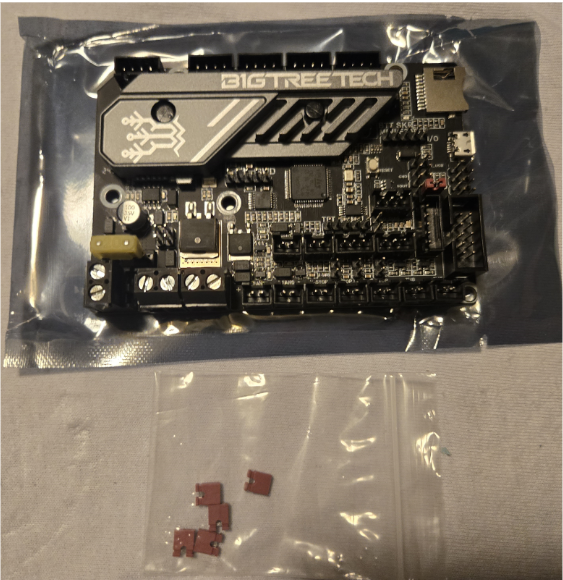
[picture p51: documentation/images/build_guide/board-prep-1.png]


- Install 3 jumpers as shown to enable sensorless homing.

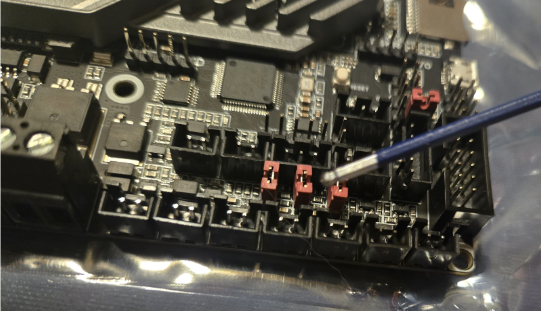
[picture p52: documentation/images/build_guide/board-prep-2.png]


- Install the SKR board by the 2 round power switch and power jack openings using 3, **M3x10mm**
>[!NOTE]
>Ignore the power wires for now, images were re-used.


- Make sure the Micro-USB and MicroSD ports line up with the holes for them in the side panel.  If needed use a file/knife/debur tool to widen the openings to allow access.

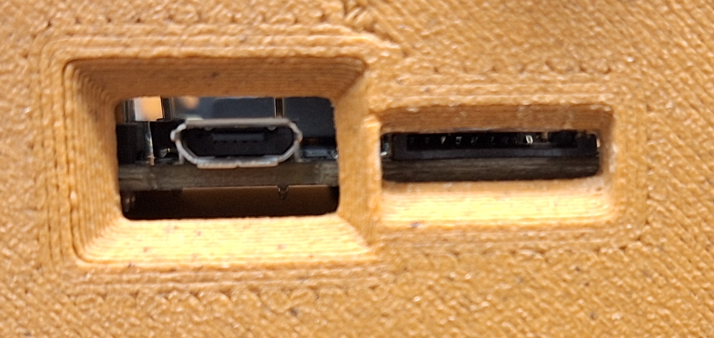
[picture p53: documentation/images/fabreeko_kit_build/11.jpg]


[Jump to Top](#top)

### Power Switch and Jack
>[!NOTE]
>Exact wiring of the switch and jack may differ.  Some switches take an extra hot in to power a LED.

>[!CAUTION]
>LDO v2.6 kits should not have this issue. LDO v2.5 kits often had 2 power jacks included only one will fit the included power supply.  Test fit the jacks to the power supply, the other will not be needed.  

Next install the **power jack** and **switch**. 

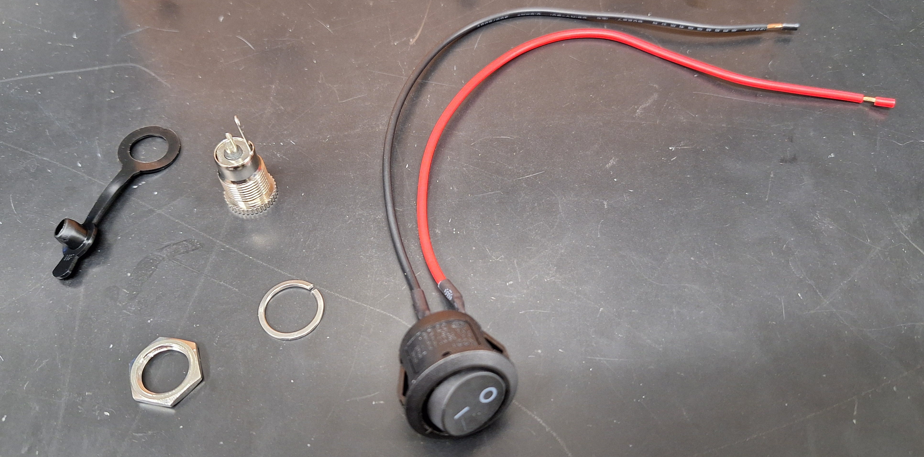
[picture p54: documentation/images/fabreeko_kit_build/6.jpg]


- There are two circular holes next to each other on [*Side-B*](../STLs/Frame/BBProV25fl_Side-B.stl) of the printer. 
- The black rubber cover for the power jack is optional
- Secure the power jack with the supplied nut
- The power switch should only fit in one way, with the LED up and will lock into place once pushed in.
  
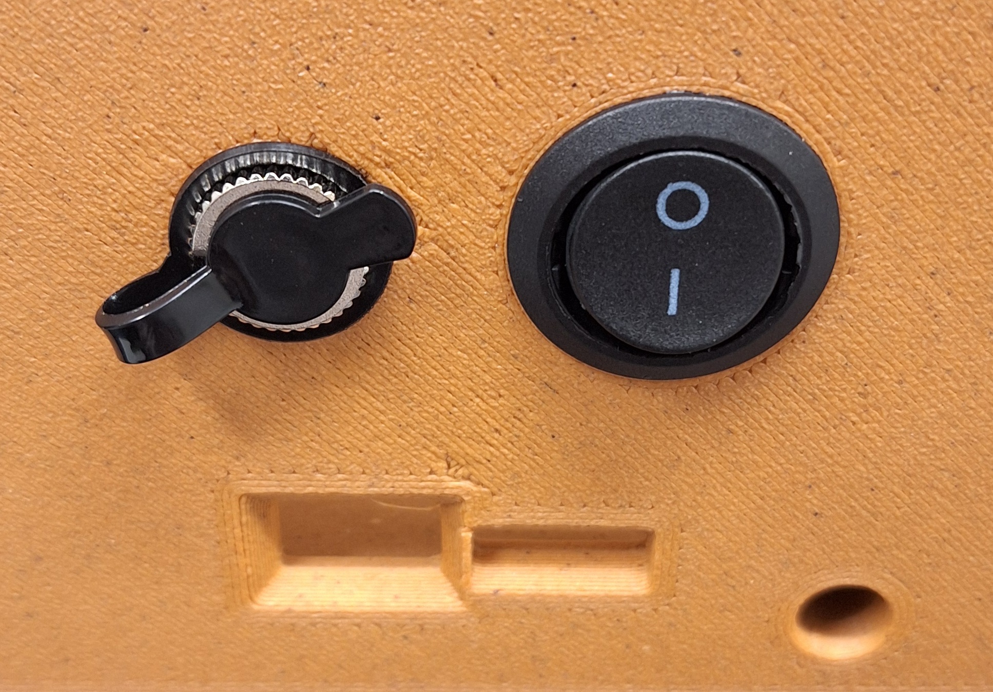
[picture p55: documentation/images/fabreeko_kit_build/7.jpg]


Here is what it should look like from the other side. 

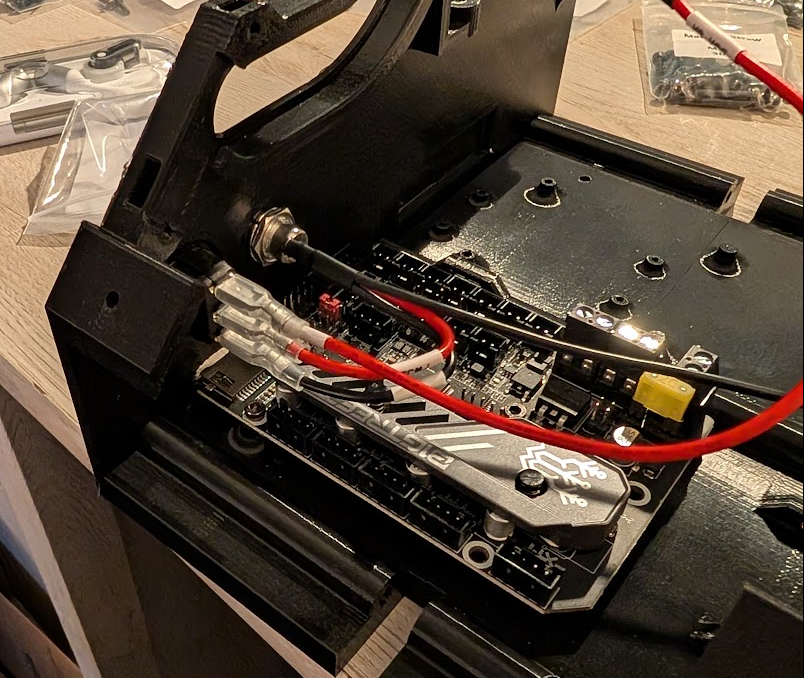
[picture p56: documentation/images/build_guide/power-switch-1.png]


>[!TIP]
>If you are planning to install a buck converter to power a pi for [klipper firmware](#klipper-extras) or octoprint for marlin this is a good time to add wago 221 connectors and optionally crimp on ferrules for splicing.

- Connect the wires from the power switch & power jack to the SKR board as shown below.  Grnd/black wire should be nearest the corner/edge(rear/scraper side of the printer), +24v/red wire goes nearest to the fuse/rest of the board(front/screen side of the printer).

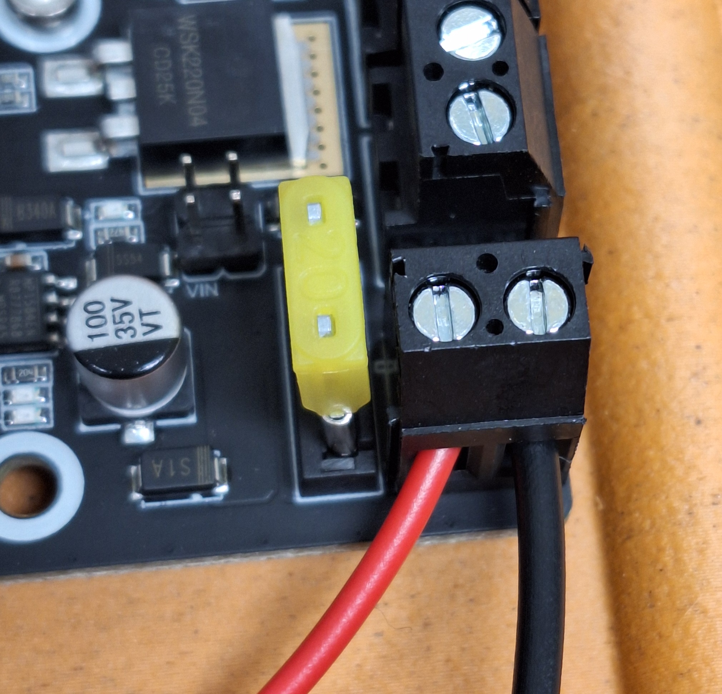
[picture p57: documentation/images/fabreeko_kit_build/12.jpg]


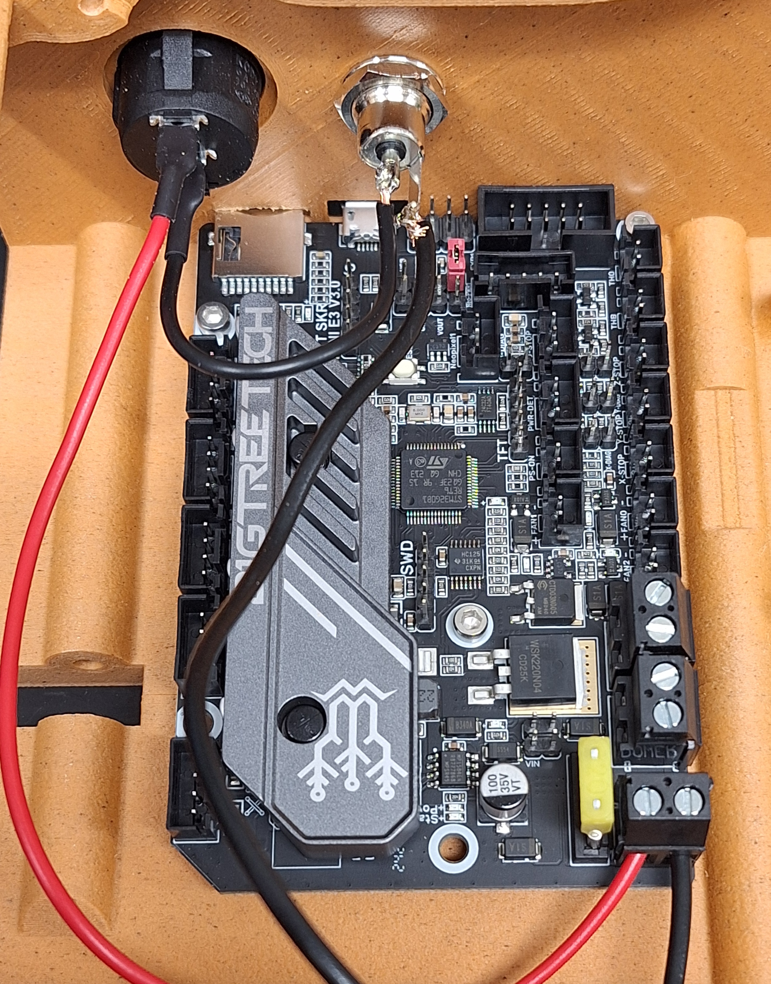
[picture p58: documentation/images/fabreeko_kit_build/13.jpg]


- Now is a good time to connect the power supply, turn it on and see if the board gets lights to confirm your wiring. Turn the switch off, unplug the PSU and continue.

[Jump to Top](#top)

### Screen Mount

Next we will install the screen. 

- Double check that all support material has been cleaned off of the screen mount.

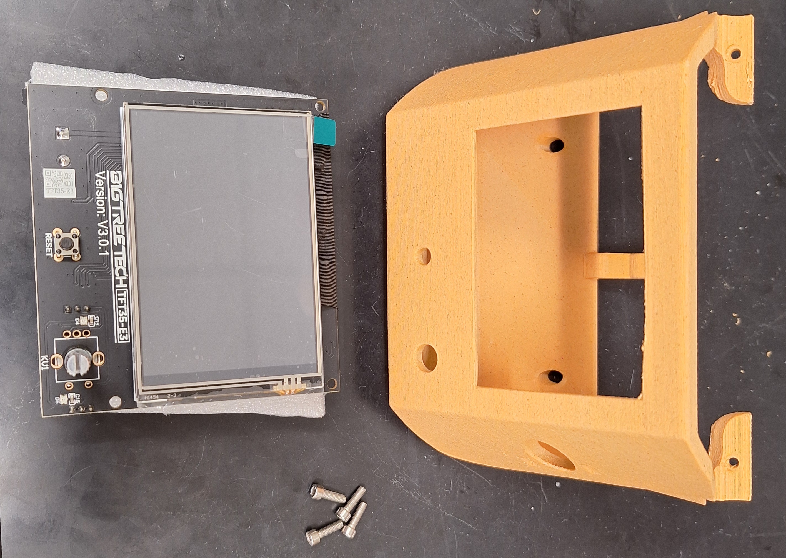
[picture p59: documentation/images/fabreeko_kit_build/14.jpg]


- Slide the screen into the inside of the [*Screenmount*](../STLs/Frame/%5Bs%5D_BBProV24fl_Screenmount.stl).  Using the holes in the bottom to allow your driver to reach, secure from the back with 4 M3x10 screws.  Do not fully tighten the screws until you have all 4 in.  Make sure the knob does not bind in click mode as this will happen if the screen is not aligned properly.  Use 4, **M3x10mm** to connect the screen to the 

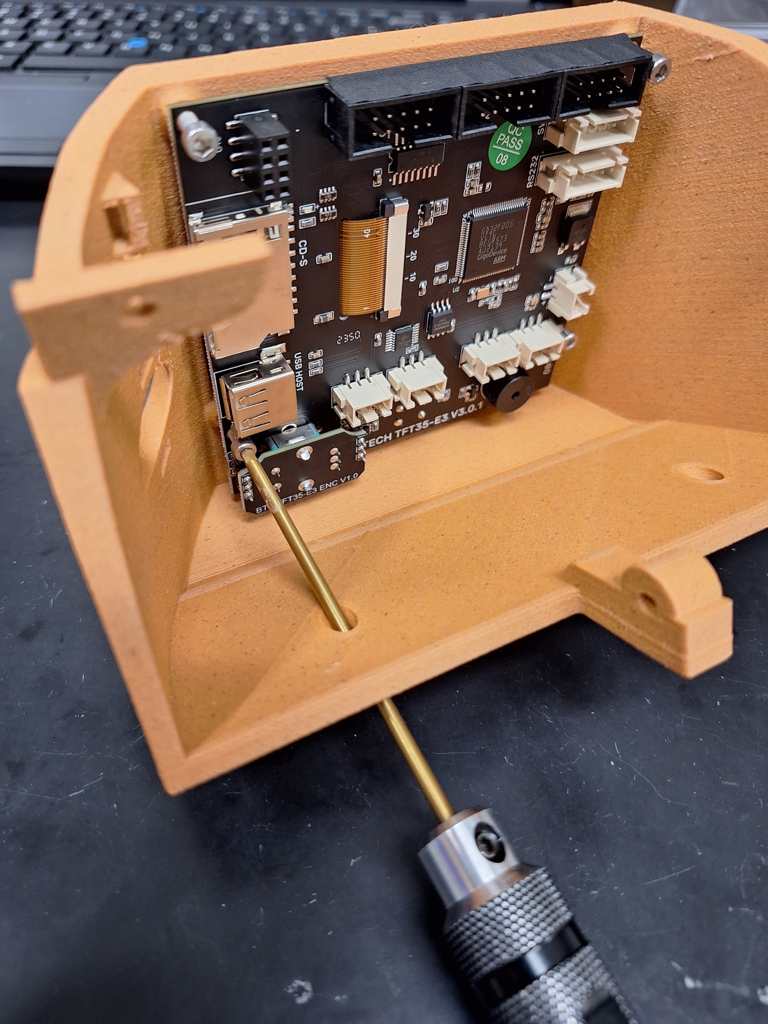
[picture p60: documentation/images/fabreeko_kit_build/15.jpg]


- Turn the mount around and attach the knob by pushing it onto the silver dial beneath the screen

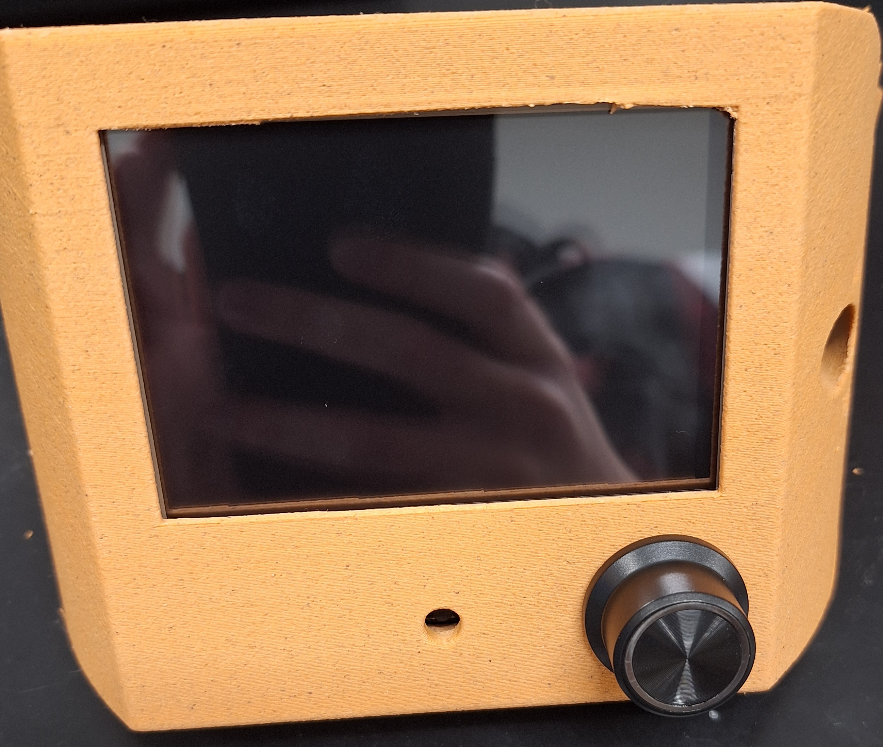
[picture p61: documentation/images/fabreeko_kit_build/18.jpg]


- Plug the wire into the port labeled RS232 on the back of the screen using the black plastic connector that combines all the wires into one.

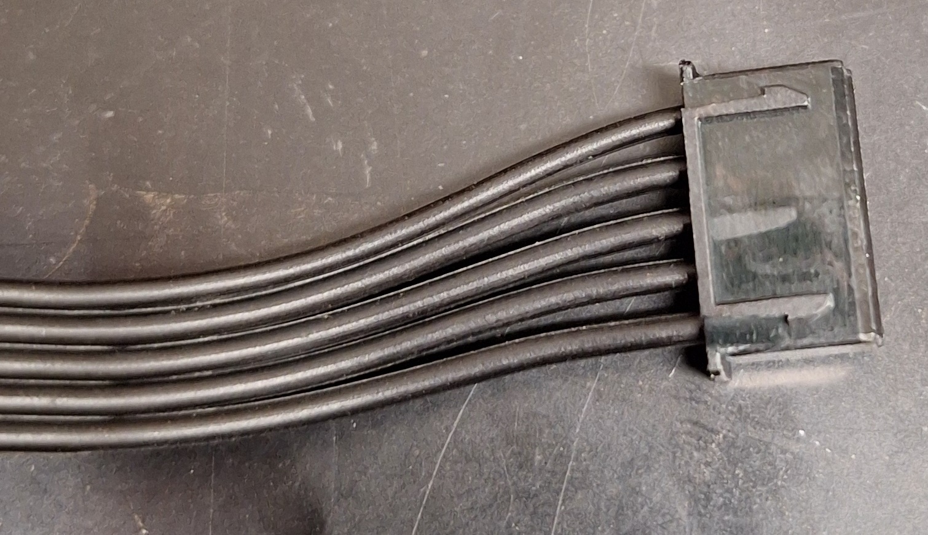
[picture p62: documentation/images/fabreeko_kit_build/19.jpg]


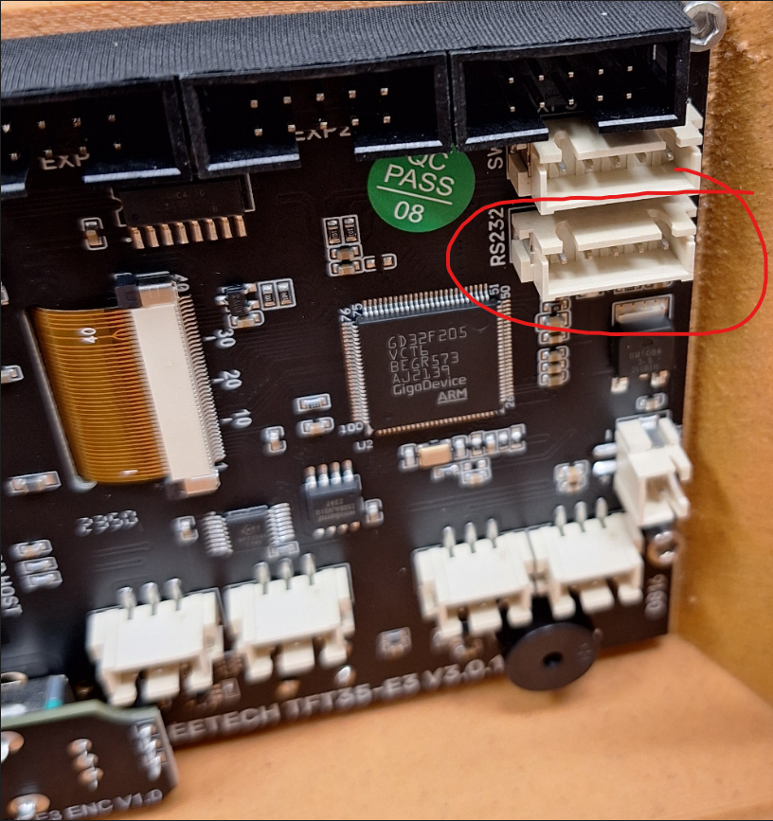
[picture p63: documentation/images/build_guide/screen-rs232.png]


- Take the printer base and flip it over.  Line up the [*screen mount*](../STLs/Frame/%5Bs%5D_BBProV24fl_Screenmount.stl) to the end pf the from with the control board. Insert an **M3 Nut** into the hole on the bottom of the frame, next to where it slots into the base.

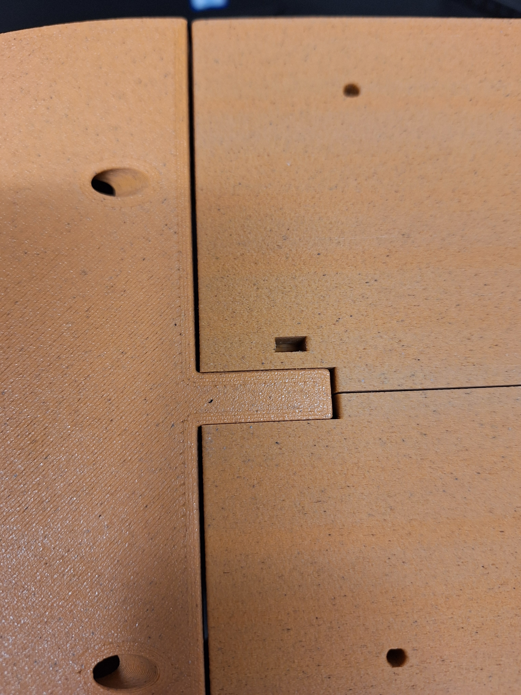
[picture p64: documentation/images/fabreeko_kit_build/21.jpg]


- Insert one **M3x20mm** into the hole on the side of the frame and use it to secure the [*screen mount*](../STLs/Frame/%5Bs%5D_BBProV24fl_Screenmount.stl)

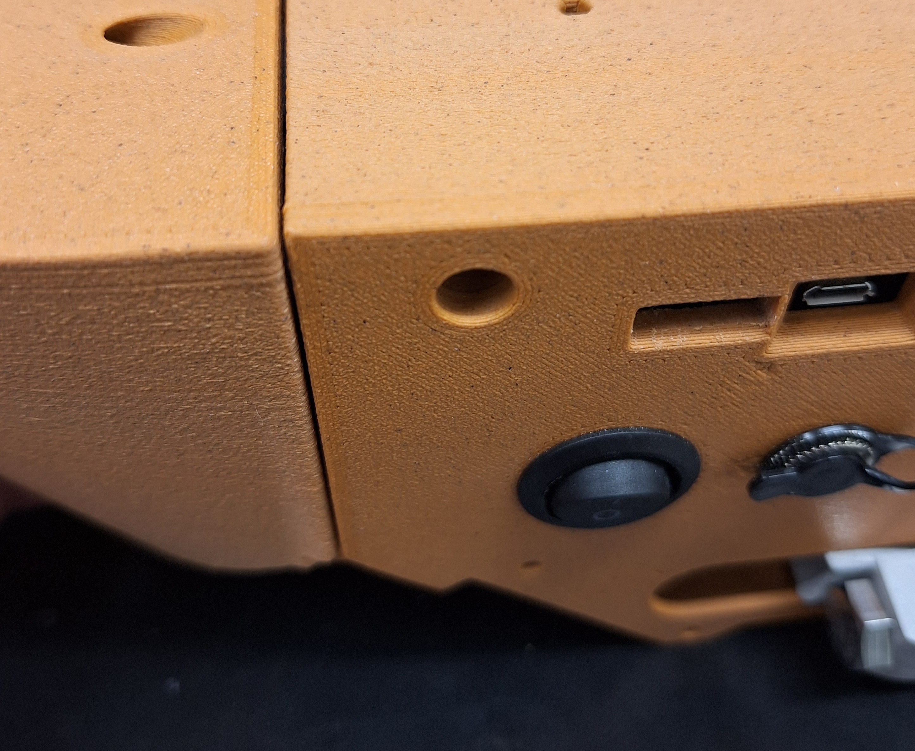
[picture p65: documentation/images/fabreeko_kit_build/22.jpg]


Next use 2, **M3x10mm screws** and 2, **M3 Nuts** to attach the screen mount with the two holes in the top. 

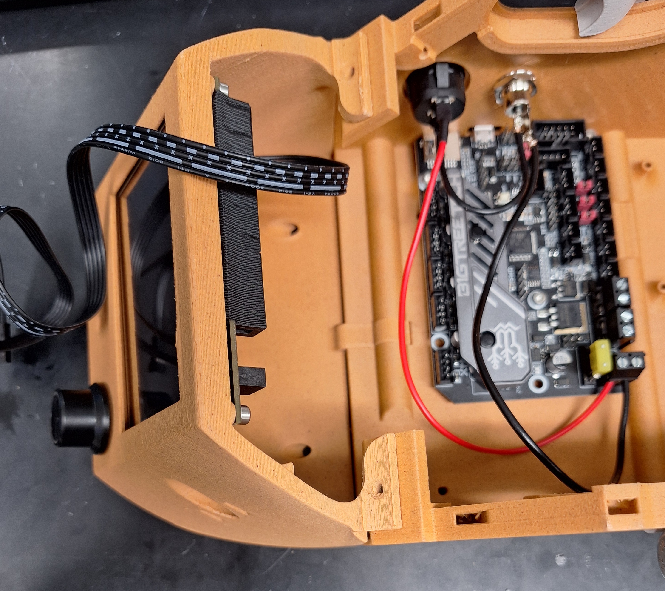
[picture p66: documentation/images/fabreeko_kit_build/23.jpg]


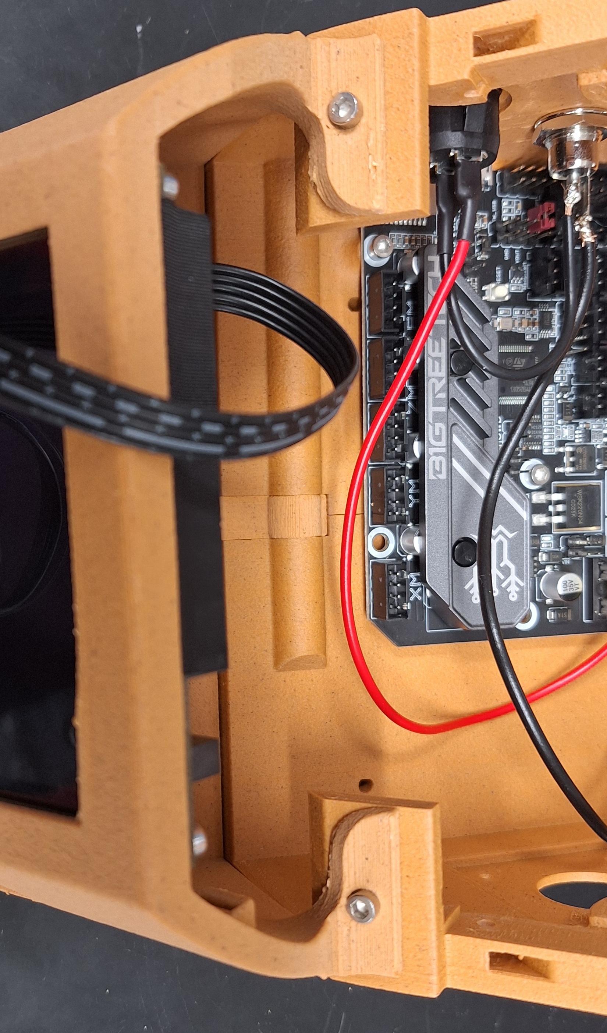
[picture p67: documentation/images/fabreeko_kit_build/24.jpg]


[Jump to Top](#top)

### Extruder
- Check your extruder manual for any particular installation considerations. 

- Attach the **gear** to the **NEMA 17 stepper motor** ensuring that the **grub screw** is tight against the flat part of the motor shaft. Make sure the gear fits properly with the rest of the gears in the extruder.  For BMG style extruders the grub screw faces AWAY from the motor body.

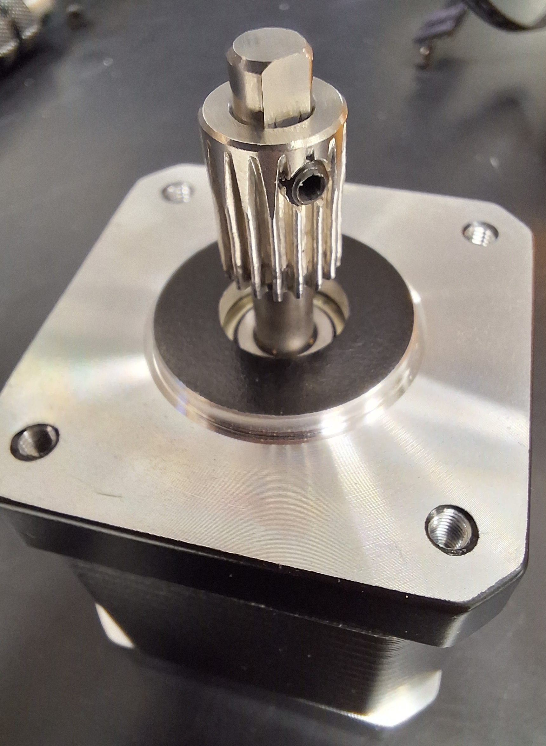
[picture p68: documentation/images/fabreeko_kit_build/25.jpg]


- Line up the motor with the mounting holes in the side of the frame.  Pay attention to the direction the motor connector is facing inside the tub.  Facing towards the screen is usually best for cleaner wiring.

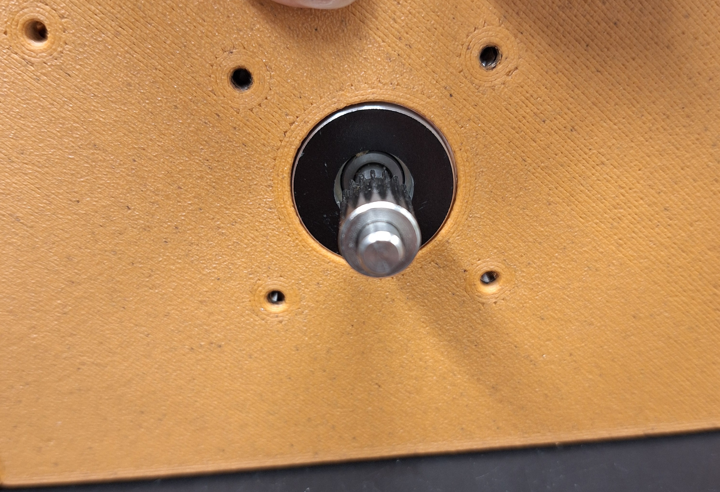
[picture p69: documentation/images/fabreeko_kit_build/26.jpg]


- Attach the extruder, with the exit path pointing towards the screen, to the outside of the frame with 3 or 4, **M3x10mm** screws depending on your extruder. LDO kit users can use the screws included with the extruder.

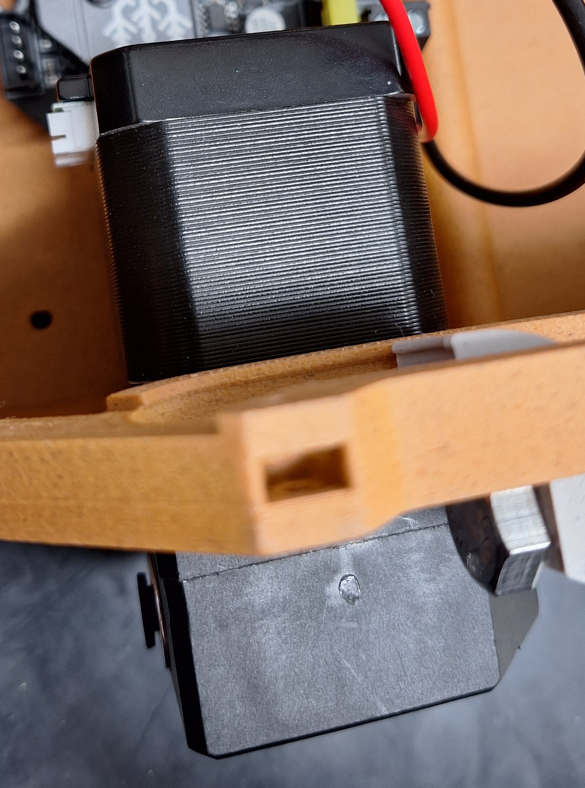
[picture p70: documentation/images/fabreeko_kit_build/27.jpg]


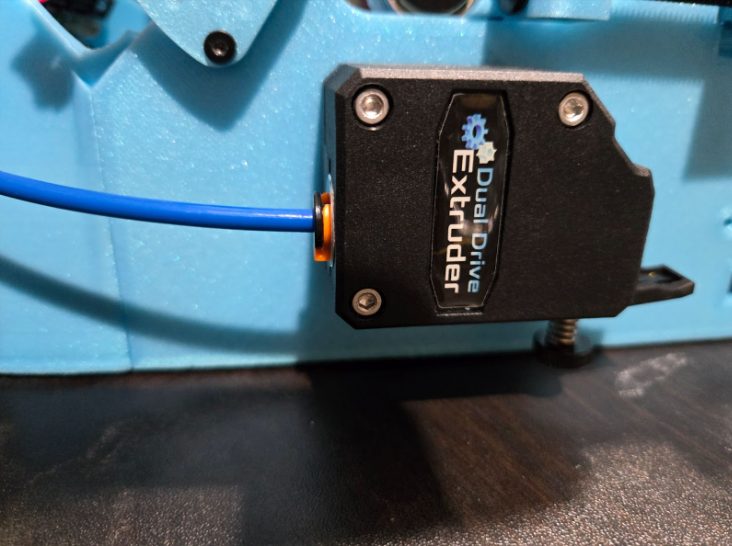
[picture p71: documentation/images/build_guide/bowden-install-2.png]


[Jump to Top](#top)

### Belt Tensioners

Next we will build and install the belt tensioners. 
>[!NOTE]
>There are two of these, one for each side, make note of the part orientation.



- Fit a **M8 Nut** into both tensioners[*PrintBelt_Pusher-A*](../STLs/PrintBelt/%5Ba%5D_BBProV25fl_PrintBelt-Pusher-A.stl)/[*PrintBelt_Pusher-B*](../STLs/PrintBelt/%5Ba%5D_BBProV25fl_PrintBelt-Pusher-B.stl)

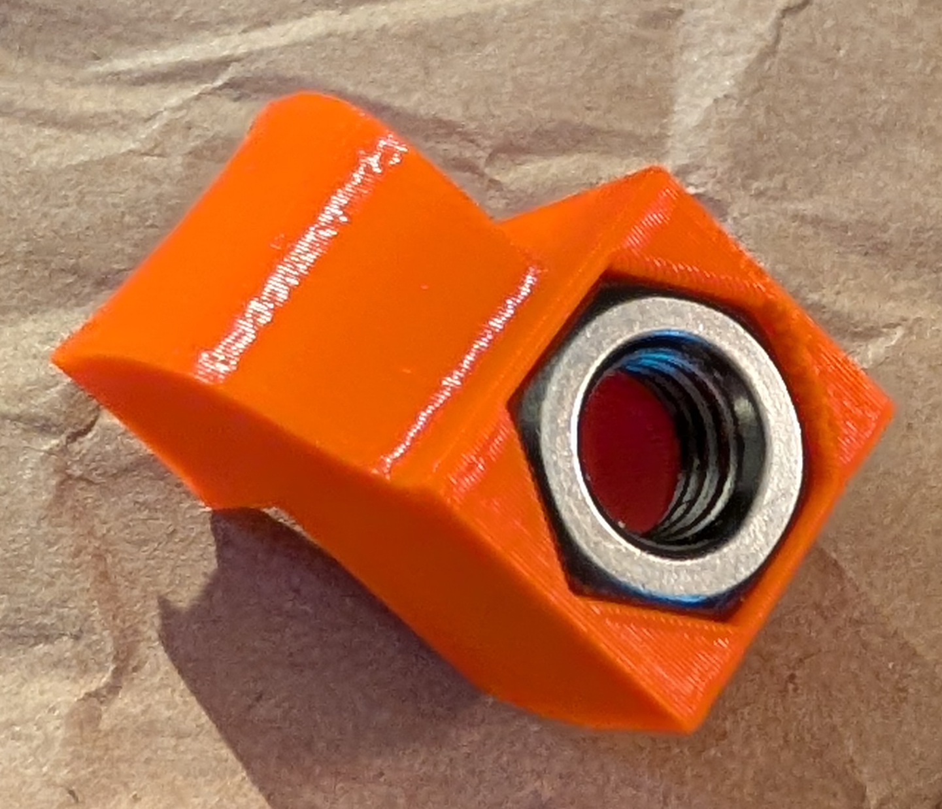
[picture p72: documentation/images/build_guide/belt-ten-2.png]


- Secure them both with a **M8x70mm** Screw 



- Fit a **M8 Nut** into each of the [*PrintBelt_Nut*](../STLs/PrintBelt/%5Ba%5D_BBProV25fl_PrintBelt-Nut(2x).stl).

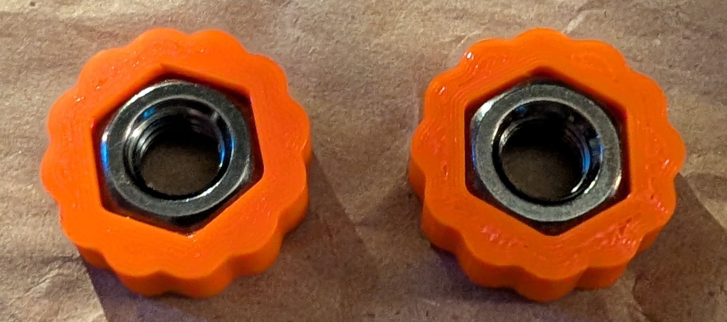
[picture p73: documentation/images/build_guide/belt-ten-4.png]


- Line up holes on each [*PrintBelt_Frame-A*](../STLs/PrintBelt/%5Ba%5D_BBProV25fl_PrintBelt-Frame-A.stl)/[*PrintBelt_Frame-B*](../STLs/PrintBelt/%5Ba%5D_BBProV25fl_PrintBelt-Frame-B.stl) with the M8 inside the [*PrintBelt_Nut*](../STLs/PrintBelt/%5Ba%5D_BBProV25fl_PrintBelt-Nut(2x).stl).

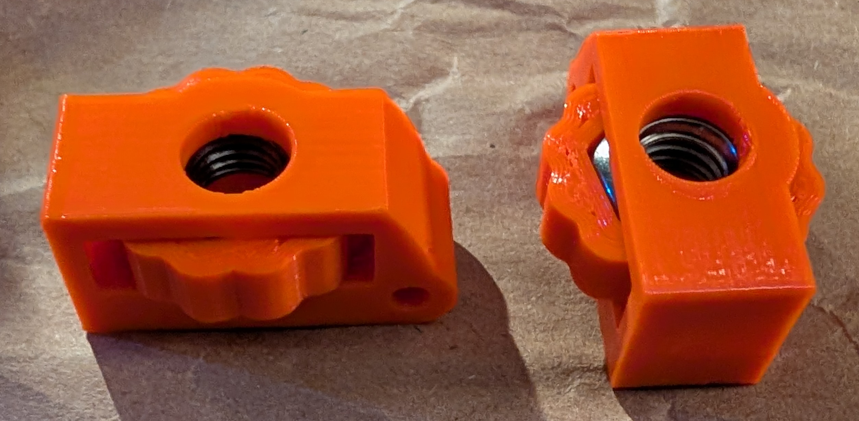
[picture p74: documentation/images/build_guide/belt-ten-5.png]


- Screw the frames onto the pushers about half way.  Make sure that the frames are facing the correct way (thicker part with m3 hole away from the pusher, side with bumps in the middle up). Make sure the correct frame is matched with the correct pushers, see image below.



- There are spots for the tensioners to fit on either side of the base. 

- Use a **M3x20mm screw** to install the tensioners into the openings on either side of the frame. The [*PrintBelt_Nut*](../STLs/PrintBelt/%5Ba%5D_BBProV25fl_PrintBelt-Nut(2x).stl) will align with the wider spot in the side openings.  The Pushers will be flat side up, curved side down. The screws do not thread into the bottom but driving it in may make it easier to guide in tight tolerances. 



[Jump to Top](#top)

### Rollers

- Check both ends of both rollers and cleanup the openings if needed.

- Wrap both [*rollers*](../STLs/ZBeltDrive/%5Ba%2Cs%5D_BBProV25fl_Roller%5Bx2%5D.stl) in electrical tape to maintain a better grip on the belt. We recommend 2 wraps in opposite spirals, the 2nd one will help hold the first in place. 

- On one of the rollers place a **M8 Nut** into the side slot. Insert a **M8x70 Hex Screw** into the [*Roller_ZGear*](../STLs/ZBeltDrive/%5Ba%5D_BBProV25fl_Roller_ZGear.stl).  Add a **608ZZ bearing** to the screw and then hand tighten the screw into the roller.

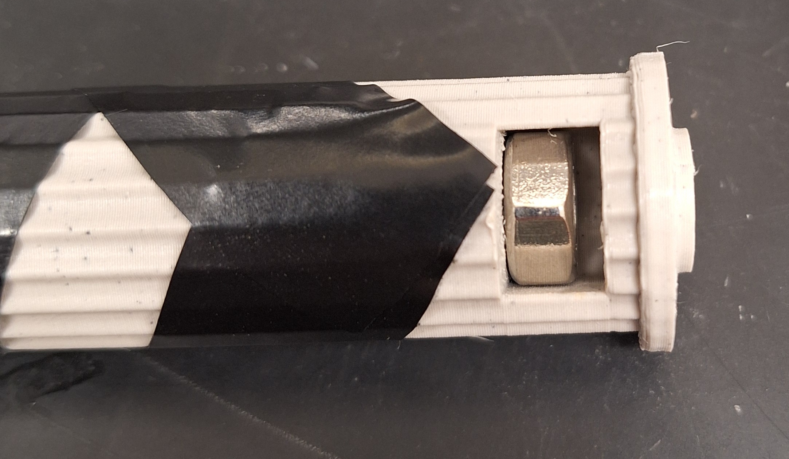
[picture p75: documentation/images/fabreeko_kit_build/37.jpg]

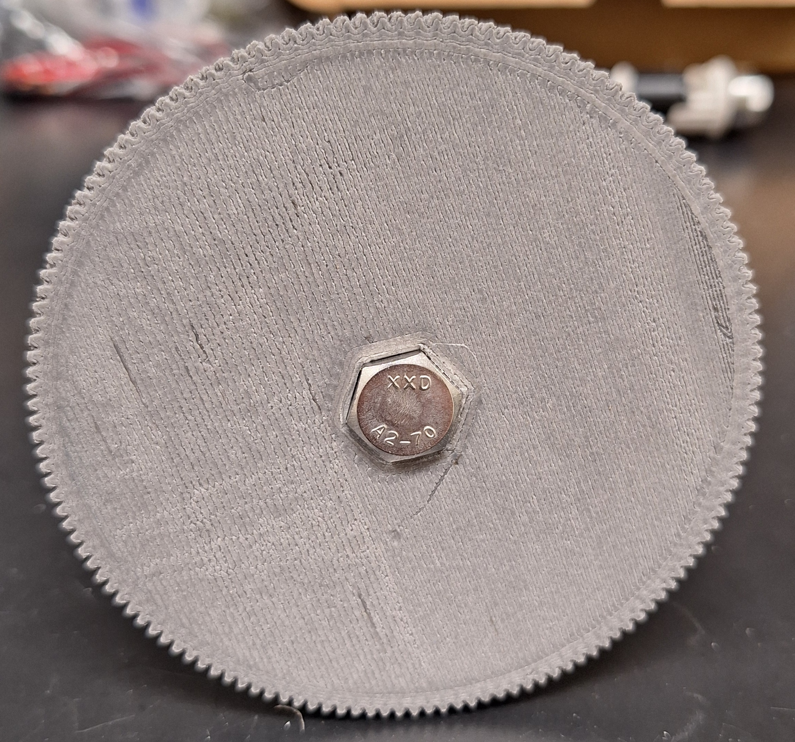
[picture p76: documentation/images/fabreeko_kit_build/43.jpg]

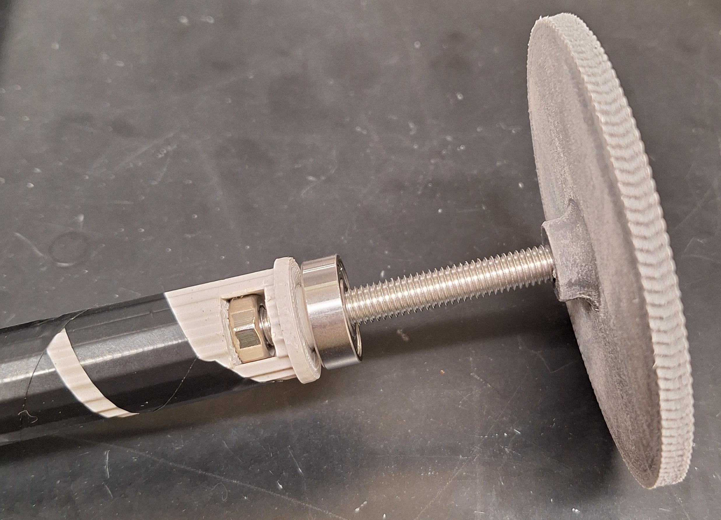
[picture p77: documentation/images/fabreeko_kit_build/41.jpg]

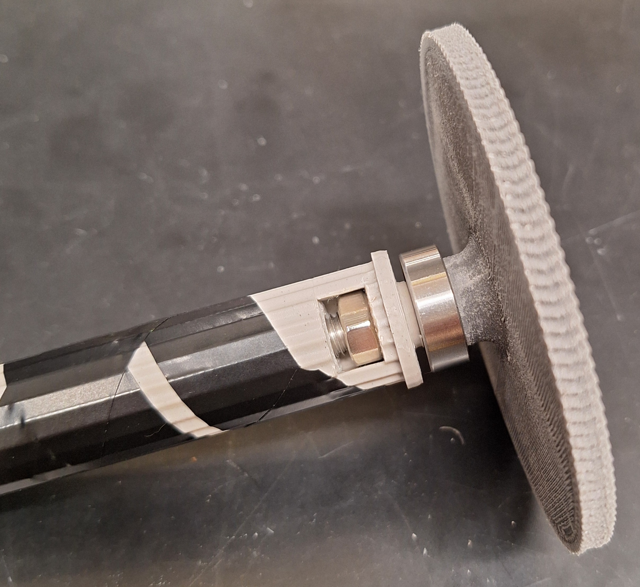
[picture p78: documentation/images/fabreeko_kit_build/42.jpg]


- For the other end of that roller and both ends of the other, place a **M8 Nut** into the side slot and then inserting a **M8x70 Hex Screw** with a **608ZZ bearing** fully into the [*roller*](../STLs/ZBeltDrive/%5Ba%2Cs%5D_BBProV25fl_Roller%5Bx2%5D.stl).  Hand tighten the screw into the roller.


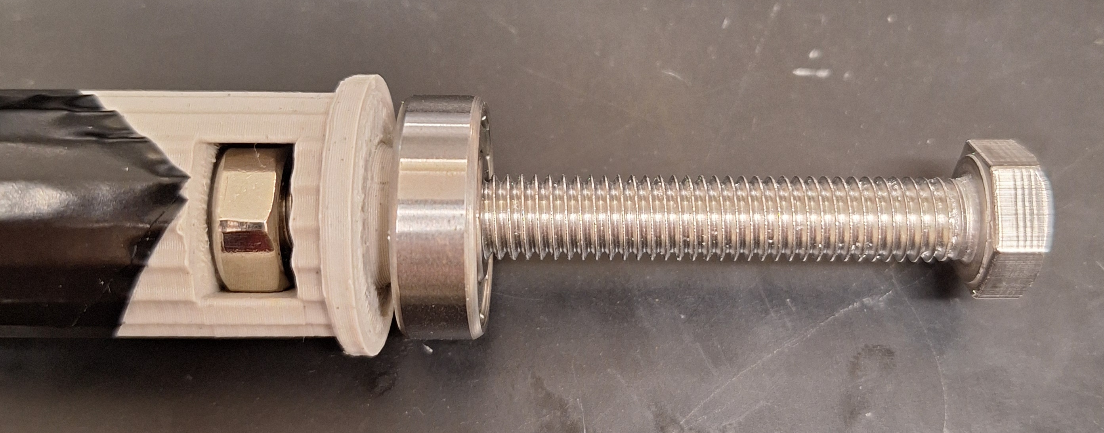
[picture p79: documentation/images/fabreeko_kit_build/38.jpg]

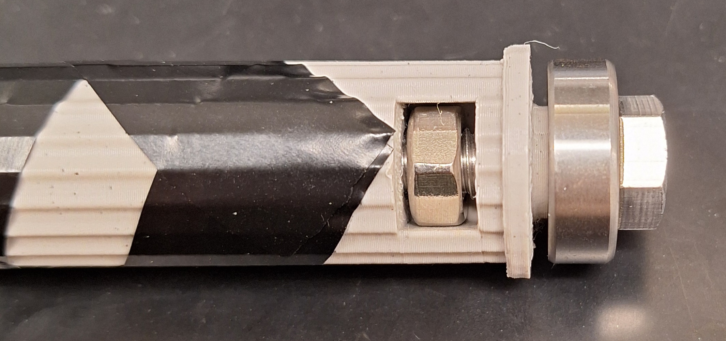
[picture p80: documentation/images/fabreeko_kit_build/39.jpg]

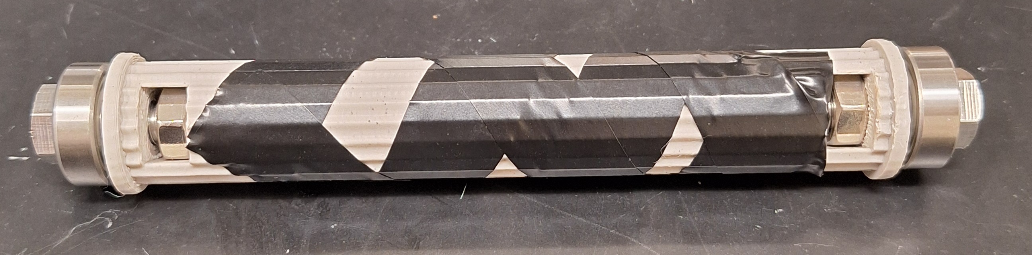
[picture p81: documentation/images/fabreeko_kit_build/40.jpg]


[Jump to Top](#top)

### Z Motor

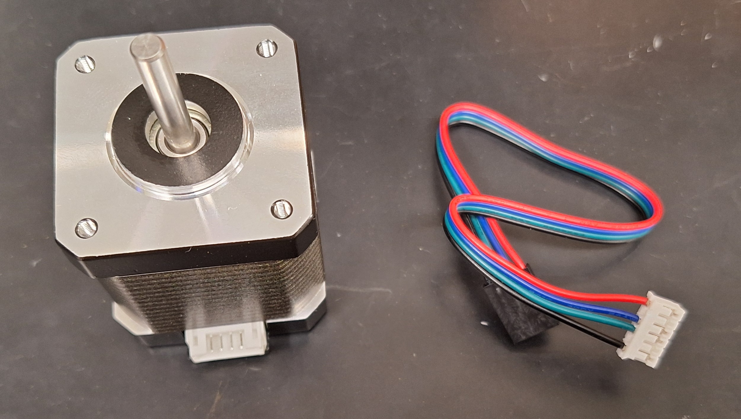
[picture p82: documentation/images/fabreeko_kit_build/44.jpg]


- Make sure the wire port on the motor is facing towards the screen 

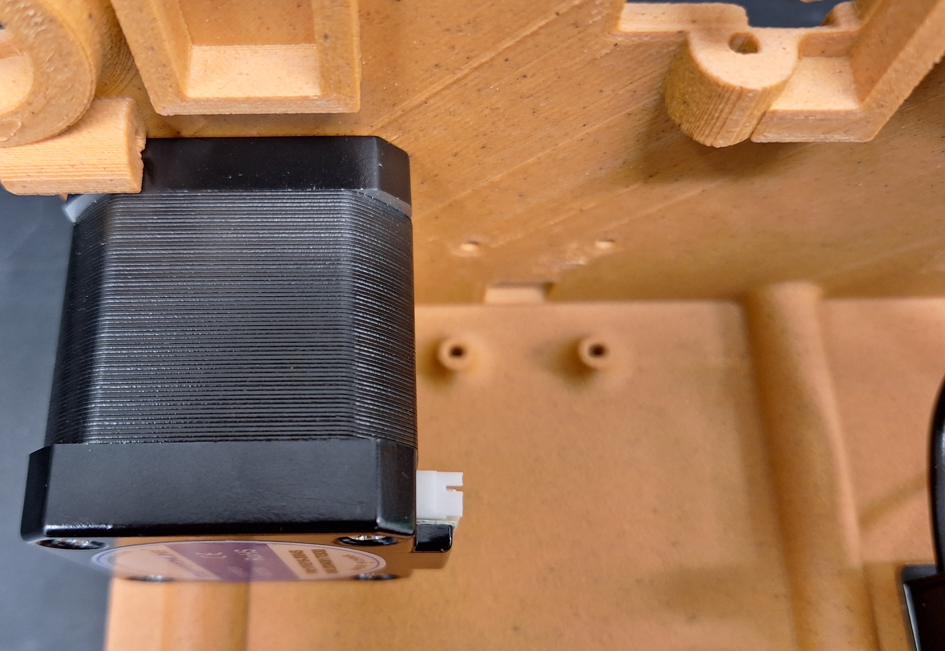
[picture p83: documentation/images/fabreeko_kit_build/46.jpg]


- Attach the Z motor to the frame using 4, **M3x10mm screws** 

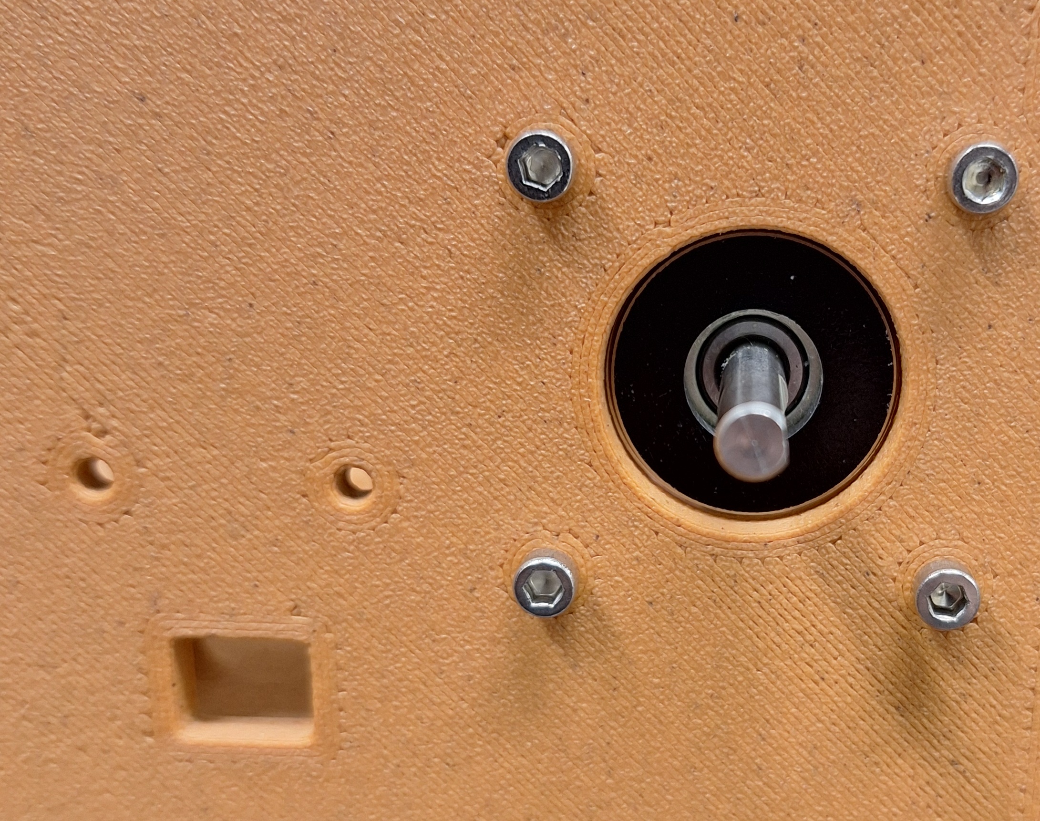
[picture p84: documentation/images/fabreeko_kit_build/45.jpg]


- Install the [*NEMA 17_Z Gear*](../STLs/ZBeltDrive/%5Ba%5D_BBProV25fl_Nema17_ZGear.stl) onto the motor and then check to make sure it lines up with the gear on the [*Roller_ZGear*](../STLs/ZBeltDrive/%5Ba%5D_BBProV25fl_Roller_ZGear.stl) we installed on one of the rollers earlier

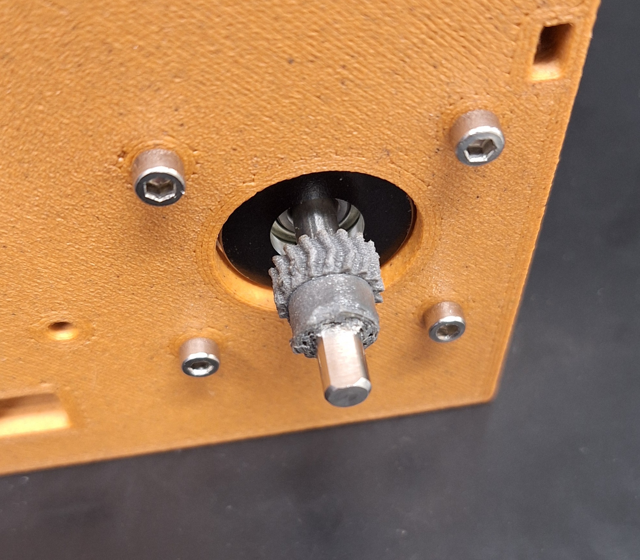
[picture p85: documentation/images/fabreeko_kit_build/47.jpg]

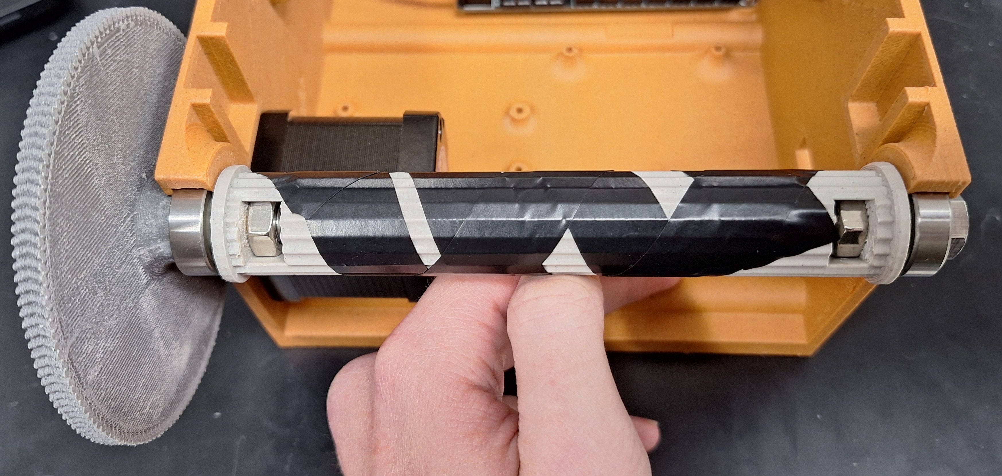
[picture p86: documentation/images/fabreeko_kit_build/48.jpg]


- Proper fit

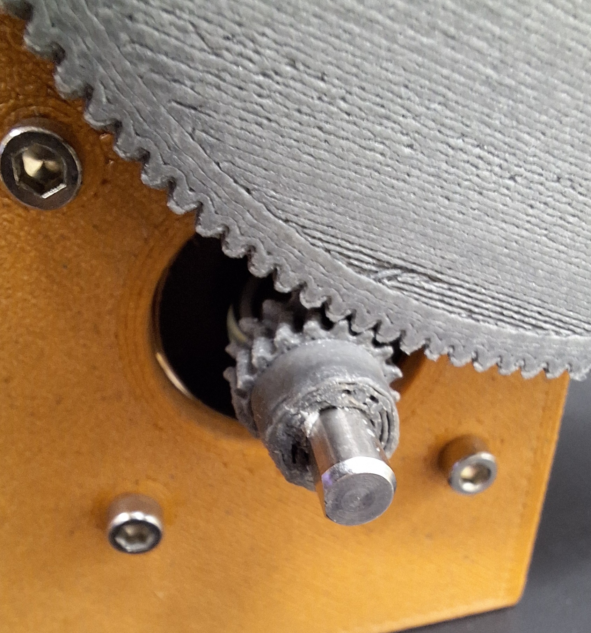
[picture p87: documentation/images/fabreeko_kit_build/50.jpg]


- Improper fit



- Take the roller back out and move on to the next step.

[Jump to Top](#top)

### Scraper Install

- If not already completed or included in a kit, follow the [Fabric Belt Guide](belt_guide.md) to make a belt.

- Place a **M3 Nut** into the slot on the side of the frame right above the motor. Repeat on the other side




- Slide the belt over the geared roller.
- Put the roller back into position, making sure the gears line up properly.
- Flip/position the belt towards the screen side of the printer.
- Use 2 **M3x20mm** to attach the scraper below the roller, securing into the nuts we previously inserted. 



- Use a **M3 Nut** and **M3x20mm** screw to attach the [*scraper*](../STLs/Frame/BBProV25fl_scraper.stl) to the frame in the same manner the screen mount.




- Flip the belt back over the scraper so it is out of your way for the next few steps.

[Jump to Top](#top)

The main body or "tub" is assembled.

## Gantry

### Install Heatsets
The v2.6 gantry assembly requires 15 M3x4x5 aka Voron Style heatset inserts.  If you are not familiar here is an old but short video that gives an overview of the process by CanuckCreator [Heatset Insert in a Minute](https://www.youtube.com/shorts/cyof7fYFcuQ).

>[!Note]
> We STRONGLY recommend running a M3x20 screw into each of these heatsets after they have cooled down.  Some of them, particularly the UnderMounts, can gather plastic on the inside and this will prevent the screws that mount the gantry to the frame from reaching the threads.

- 6 inserts go in the [X Carriage](../STLs/Gantry/X/BBProV26fl_X-Carriage.stl) as shown below. The green is from re-using heatsets, ignore it.



- 5 inserts go in EACH [[a]_BBProV26fl_XrailMountUnder-SideA.stl](../STLs/Gantry/X/[a]_BBProV26fl_XrailMountUnder-SideA.stl) and [[a]_BBProV26fl_XrailMountUnder-SideB.stl](../STLs/Gantry/X/[a]_BBProV26fl_XrailMountUnder-SideB.stl).  









>[!Caution]
> You forgot to run a M3x20 screw into each of the heatsets after they have cooled down.  Go ahead and do it now. Some of them, particularly the UnderMounts, can gather plastic on the inside and prevent the gantry mounting screws from reaching the threads.

[Jump to Top](#top)

### X Carriage

>[!CAUTION]
> DO NOT REMOVE THE RUBBER STOPPERS from the linear rail until it is necessary.  When the stoppers need to be removed to attach the rail move them down a few holes.  Be sure the carriage stays on the rail or the bearing balls will fall out making a mess and the installer miserable. 

>[!Note]
> We highly recommend lubricating **all** the linear rail bearings (visible in the photo below) using something like Mobil EP1 or EP2 grease prior to installation. Nero3D has a [great guide providing explanations and how-tos for this](https://youtu.be/UYvhYjkBFTY?si=frlAKNLAvElEVHFv) 

 - Locate [*[a]_BBProV26fl_XrailMount-SideA*](../STLs/Gantry/X/[a]_BBProV26fl_XrailMount-SideA.stl), [*[a]_BBProV26fl_XrailMount-SideB*](../STLs/Gantry/X/[a]_BBProV26fl_XrailMount-SideB.stl) and the two XrailMountUnder parts with the heatsets installed.

 - Take the cleaned and lubricated MGN12C rail, place it on a flat surface, move the carrier to the center, and carefully move the rubber stoppers from one end towards the center so the two holes are open.

>[!Note]
> The extra holes above and below the rail aligner are for backward compatability with v2.5 that used 2 MGN7H rails for X.

>[!Caution]
> You probably missed the other two reminders to run a M3x20 screw in all the heatsets you installed.  Go ahead and do it now.  It will REALLY make you mad when mounting the gantry is harder than it has to be.

 - On each side the Mount and MountUnder pieces will be aligned with the raised portion towards the inside.

 
 

- Line up the mount holes with the two end MGN12C rail holes and loosely fasten them together with **M3X10 screws**.  Slide the carrier towards that side, move the other stopper and fasten the other side.
>[!Caution]
> Leave the screws loose, you will want some play in the parts later on when you attach the gantry to the frame.




- Position [*BBProV26fl_X-Carriage*](../STLs/Gantry/X/BBProV26fl_X-Carriage.stl) over the MGN12C carrier and securely fasten it using 4 **M3x6 BUTTON HEAD** screws.  
>[!CAUTION]
> You MUST used button head screws on this, the idlers will catch on Socket head caps and cause motion issues.  Yes, they are wrong in the picture.



- On [*BBProV26fl_X-Carriage*](../STLs/Gantry/X/BBProV26fl_X-Carriage.stl) line up the **smooth idlers** with the indicated holes and hold in place with 2, **M3x20 screws**.  The screws may not thread into the back of the plate depending on your print tolerances.  That will be fine, tension will hold them well enough.



[Jump to Top](#top)

### Y Carriage
 >[!Note]
> Older MGN7 sized parts may be shown, for 2.6 the overall process and part layout are the same with larger mgn9c and M3 BHCS attachment hardware.
 
 - Attach the [*YCar_Bam_Fan*](../STLs/Gantry/Carriage/Bambu/%5Ba%5D_BBProV25fl_YCar_Bam_Fan.stl) to the [*YCar_Bam_BeltHolder*](../STLs/Gantry/Carriage/Bambu/%5Ba%5D_BBProV25fl_YCar_Bam_BeltHolder.stl) by inserting 2, **M3x10 screws** into the holes indicated in the first image, and through the whole in the second image
- Secure with **M3 Nuts** 






- Orient the fan so that the air flow will move towards the air duct on the fan mount, then secure where indicated with zip ties 



- Use a zip tie to secure the wires to the side of the carriage 



>[!CAUTION]
> DO NOT REMOVE THE RUBBER STOPPERS from the linear rail until it is necessary.  When the stoppers need to be removed to attach the rail move them down a few holes.  Be sure the carriage stays on the rail or the bearing balls will fall out making a mess and the installer miserable. 

>[!Note]
> We highly recommend lubricating **all** the linear rail bearings (visible in the photo below) using something like Mobil EP1 or EP2 grease prior to installation. Nero3D has a [great guide providing explanations and how-tos for this](https://youtu.be/UYvhYjkBFTY?si=frlAKNLAvElEVHFv) 

>[!Note]
> For the Y carriage sides in the next few steps LDO kit users planning to use the ECAS connector will be using the ECAS version of the parts.

- Insert a **M3 Nut** into this slot on the [*[a]_BBProV26fl_YCar_Bam_SideA*](../STLs/Gantry/Carriage/Bambu/[a]_BBProV26fl_YCar_Bam_SideA.stl)



- Attach the carriage to the **MGN9C linear rail** using 4, **M3x6mm BUTTON HEAD screws**.  



- Insert a **M3 Nut** into the still exposed slot on the [*YCar_Bam_Side-A*](../STLs/Gantry/Carriage/Bambu/%5Ba%5D_BBProV25fl_YCar_Bam_SideA.stl)




- It should line up with the hotend fan as shown below.  If everything looks good sit this part aside for now and continue on.



#### Bowden Connector
>[!Note]
> No installation pictures for this step at the moment

- Install the bowden coupler into [*YCar_Bam_SideB*](../STLs/Gantry/Carriage/Bambu/[a]_BBProV25fl_YCar_Bam_SideB.stl)





[Jump to Top](#top)

- Insert **M3 Nuts** into the slots indicated on the [*YCar_Bam_Side-B*](../STLs/Gantry/Carriage/Bambu/%5Ba%5D_BBProV25fl_YCar_Bam_SideB.stl)


 

Next we will install the hotend to the [*YCar_Bam_Side-B*](../STLs/Gantry/Carriage/Bambu/%5Ba%5D_BBProV25fl_YCar_Bam_SideB.stl)



- Use a **M3x20mm screw** and a **M3 Nut** to attach the hotend to the [*YCar_Bam_Side-B*](../STLs/Gantry/Carriage/Bambu/%5Ba%5D_BBProV25fl_YCar_Bam_SideB.stl)
through the hole shown at the top.  Make sure the wire groove of the hotend heat sink is facing up/the short side of the plastic part.




- Make sure the screw goes through the correct hole on the hotend
>[!NOTE]
>This is not a captive nut, the hotend will be held more firmly by the fan later.



- Insert **M3 Nuts** into the holes pictured 

 
 


- Attach the hotend fan assembly to the rail carriage using **M3x10mm screws** (this is easier to do one half at a time)

 
 
 


[Jump to Top](#top)

### Hotend Electronics
>[!CAUTION]
> Resist the urge to install the silicon sock on the hotend. It will hit the bed before the nozzle reaches and make bad stuff happen.

- Locate the hotend heater cartridge, thermistor, and clip. 



- Apply a small amount of thermal compound to the thermistor bulb.

- Insert the **thermistor** into the small hole in the block right above the nozzle and run the wire through the channel built into the black **heat break**. 



- Apply a thin coating of thermal paste to the flatter side of the **heater cartridge**
- Place the **heater cartridge** on the front of the block and run the wires through the same channel as the thermistor
- Secure it and the thermistor in place with the **metal clip** 



[Jump to Top](#top)

### Heatbreak Fan

- Locate the **heatbreak fan**. 



- Using 2, **M3x20mm screws** in the top hole into the captive nuts



- Use 2 **M2.5x14mm** screws in the bottom holes to secure the fan to the heat break.  These screw will cut into the metal.



[Jump to Top](#top)

### Y Tensioner
- Gather the [*TensionIdlerHolder*](../STLs/Gantry/Y/%5Ba%5D_BBProV25fl_RockMonsterNo1YTentionerIdlerHolder.stl), [*TensionBody*](../STLs/Gantry/Y/[a]_BBProV26fl_RockMonsterNo1YTentionerBody.stl), [*TensionerNut*](../STLs/Gantry/Y/%5Ba%5D_BBProV25fl_RockMonsterNo1YTentionerNut.stl), an idler, and a M3x20 SHCS.



- On [*TensionIdlerHolder*](../STLs/Gantry/Y/%5Ba%5D_BBProV25fl_RockMonsterNo1YTentionerIdlerHolder.stl) and  [*TensionBody*](../STLs/Gantry/Y/[a]_BBProV26fl_RockMonsterNo1YTentionerBody.stl) note that there are counterbores.  We will use these to align the parts properly.



- Insert the [*TensionIdlerHolder*](../STLs/Gantry/Y/%5Ba%5D_BBProV25fl_RockMonsterNo1YTentionerIdlerHolder.stl) into the [*TensionBody*](../STLs/Gantry/Y/[a]_BBProV26fl_RockMonsterNo1YTentionerBody.stl) with both counterbores facing upward.



- Slide the idler into the [*TensionIdlerHolder*](../STLs/Gantry/Y/%5Ba%5D_BBProV25fl_RockMonsterNo1YTentionerIdlerHolder.stl), then insert a **M3x20mm screw** to hold it in place. The **M3x20mm screw** will stick out the bottom, this keeps the idler and holder from sliding out.





- Screw the [*TensionerNut*](../STLs/Gantry/Y/%5Ba%5D_BBProV25fl_RockMonsterNo1YTentionerNut.stl) on the [*TensionIdlerHolder*](../STLs/Gantry/Y/%5Ba%5D_BBProV25fl_RockMonsterNo1YTentionerIdlerHolder.stl) a couple threads to hold everything together.



[Jump to Top](#top)

### Y Axis

- Attach the linear rail of the Y axis to the inside of the Y Tensioner using 2, **M3x10mm screws** and 2, **M3 Nuts**.  Insert the screws in on the rail side.  If your Hex key/driver is long enough go through the holes on the opposite side to get them tight.



- Attach the linear rail of the Y axis to the X gantry as shown below, using 2, **M3x10mm screws** and 2, **M3 Nuts**



- Attach the [*BBProV26fl_LinearRailReplacement*](../STLs/Gantry/Y/BBProV26fl_LinearRailReplacement.stl) on the other side of the Y axis using 4, **M3x10mm screws**



[Jump to Top](#top)

### Y Axis GT2 Belt

- Pre-cut two belts to 480mm (Y axis) and 290mm (X axis).  These will be a little long. 
 
- Run the longer (Y) belt through the Y tensioner, teeth facing toward the idler, and secure the first 3 teeth into the Y gantry





- Loop the belt around, insert as much belt as you can fit into the remaining teeth. Leave the belt lay for now, we will grab it with a pulley and cut it to length later.



[Jump to Top](#top)

### Mount Steppers
- Locate the 2 **NEMA11 motor** and 2 **toothed pulley**. 



- Install the **pulley** onto the motor shaft so there is about 7.5mm between the motor block and toothed section of the pulley. Also make sure one **M4x4 grub screw** is on the flat face of the shaft.

- Repeat the pulley installation on the second motor.





- Sit the two motors in a row with wires facing to the left.  Place [BBProV26fl_X-CarraigeMotorMount](../STLs/Gantry/X/BBProV26fl_X-CarraigeMotorMount.stl) on top of the motors with the pocketed side down.  Secure both to the mount with 4, **M2.5x6mm screws** in each motor.



- The motor on the wider end will be your Y motor and go towards the hotend, the motor on the more narrow end will be the X.

[Jump to Top](#top)

### X Axis GT2 Belt

- Locate the two sets of [*X_PivotArm*](../STLs/Gantry/X/%5Ba%5D_BBProV25fl_pivotArm(2x).stl) and [*X_Pivot Clamp*](../STLs/Gantry/X/%5Ba%5D_BBProV25fl_XPivotClamp(2x).stl).  **Loosely** assemble the two pieces using 2 **M3x10 screws** and **M3 Nuts**.



- On the right side, paying attention the the orientation of the belt teeth, feed the belt between the two pieces and out through the opening nearest the screws on the [*X_Pivot Clamp*](../STLs/Gantry/X/%5Ba%5D_BBProV25fl_XPivotClamp(2x).stl).  Pull 5 or 6 teeth worth of belt through and tighten the 2 **M3x10 screws** to secure the belt.

- Push the loose end of the belt through the slot in the gantry with the teeth facing toward the hotend.



- Attach the [*X_PivotArm*](../STLs/Gantry/X/%5Ba%5D_BBProV25fl_pivotArm(2x).stl) on the right side of the assembly using a **M3x20 screw** 



- Thread the loose end of the belt through the X carriage on top of the two idlers and out the slot on the left side.



- Using a wrench, screwdriver, or something pull a loop the X belt to the bottom of the carriage.  We need to have a loop large enough that the X motor pulley can pass.



#### Tricky Part

- Grab your mounted motors, hold them pulleys down with the wide end facing the hotend.

- Loop the Y belt around the upper motor.



- Lower the motors down in to place.  If your X belt is tucked nicely around the outside the pulley should fit down with minimal wiggling.



- Grab the X belt on the left side of the gantry and pull out any slack.  Keeping it taught (no need to be forcibly tight) move the gantry back and forth.  It should move smoothly with slight resistance and sound from the stepper.

- Assuming things are moving freely, fasten the motor mount bracket to the gantry using 6 **M3x20 screws**.



- Feed the loose end of the belt through the other pivot clamp, leaving it loose.



- Attach the pivot clamp to the gantry using a **M3x20 screw**.



- Push both pivot clamps against the gantry as shown.  This is the point where these add the least amount of pull to the belt.



- Pull as much slack as possible out of the X belt.  You might need to push it in from the inside and help guide it through. Tighten the screws to hold the belt.



- On each side install a **M3x20 screw** and **M3 nut**, these are used to tension the belt.



- Evenly tighten those screws to tighten the X belt.  It only needs to be tight enough that the belt does not slip on the motor pulley during a rapid move.

- Once the belt is tight, move the gantry all the way to each side, ideally the idlers will hit the side before the gantry hits the screws.  If the screws hit first, release the tensioning screws on both sides, release the belt clamp screws on the left side and try to get another tooth or two fed through.  Repeat the checks as needed.

- Trim any excess off the end of the X belt.  Leave 6 or so teeth extra to make reinstalls easier if you need to do repairs.

[Jump to Top](#top)

### LDO Toolboard

- Before installing the the toolboard, shorten the Y axis belt with the tentioner loose.  After cutting and re-inserting the belt back into the teeth, secure it wiht a zip tie.



- If building from an LDO kit locate the printed [*LDO Toolboard mount*](../STLs/Gantry/Y/LDO%20Kit%20-%20Toolboard%20Mount%20v1.stl) and install it by removing the top two screws from the **Y Carriage**, align the mount as shown and replace the screws.  

- Use a pair of **M3x10 screws** to fasten the toolboard to the mount.
>[!Note]
>The LDO BOM was finalized before the introduction of the toolboard.  There is a chance of being short a couple M3x10 screws however most kits seem to have a couple extras.

- Connect the Parts Cooling Fan to the PCF port, Hotend Fan to HEF port, Hotend Thermistor to TH0 port, and Hotend Heater to the HE0 port on the board.



[Jump to Top](#top)

### Gantry Completion

- Before the gantry is attached it is helpful to pre-place a couple zip ties.  Install them in a VERY loose loop,  NOT cinch then down.  One zip tie goes inside the screen mount, pointed out by the key in the image below.  This will hold the wires coming from the X and Y Motors.



- Install another zip tie, again in a VERY loose, in one of the holes to the opening on the right side of the screen mount.  This will hold the wires coming from the hotend.



- Install the bowden tube in the carriage and install the locking clip behind the collet.  It might be easier to loosen the Y belt a little so you can get fingers in there.  Sometimes a pair of needle-nose can assist in installing the clip.  It is a little tight.  



- Move the gantry on both the X and Y axis.  There should be smooth motion in both directions for the full range.  The belts should be tight enough that they do not slip on the pulley during a rapid movement.  Overtight belts can cause restricted or rough movement by adding torsion to the frame.  Adjust X or Y Tensioners as needed.

- On both Side A and Side B insert 1 **M3 nuts** into the gantry positioning holes on the front of the pan as shown below.



- If needed, push the nuts completely into the holes using a 2mm Hex key (same size used to drive M2.5 screws).  Then, use the key to make sure the nuts are aligned by pushing it through the frame openings.

>[!Note]
> If you ignored us eairlier and tightened the screws holding the rails to the gantry brackets go ahead and loosen them up now so you do not break the parts pushing them over the frame.

- Slide the gantry over top of the frame, line up the upper gantry mounting holes with the top (Pointy end) holes on both sides of the gantry. Install a **M3x30 screw** into this hole on each side.  Do not tighten completely.



- Tilting the gantry to line up the other gantry mounting hole in the frame with the hole marked 45 install a second **M3x30 screw** in each side.
>[!NOTE]
>This is easy to change later if printing at 30 degrees, 45 gives more room to complete the build.



- Tighten down all 4 gantry mounting bolts.

- Tighten down all 4 of the X axis linear rail bolts we left loose eairlier.



- Put the bowden tube into the extruder, secure with a clip.



- The gantry and frame assemblies are now complete and joined.

[Jump to Top](#top)

## Heated Bed

Having a heated bed is completely optional.  This step may vary depending on how the bed is sourced.  Three options will be listed out 1) No bed heater, 2) LDO Kit , 3) Fabreeko Kit.  Assemble the bed using the appropriate steps below and then set it aside to complete most of the wiring before putting the bed and belt in place and covering everything up.

>[!NOTE]
>Newer versions of the bed plates have holes and nut capture reliefs in each of the 4 wings the bed plate uses to rest in the tub.  These screws are used to level the bed if needed.  A **M3x20 screw** is placed through the hole pointing down, a **M3 nut** is spun on to the bottom of the screw.  The nut will fit into the capture relief and as the screw is turned to the right the nut moves up the screw lifting that section of the bed up.

### No Heated Bed

- Find the [[HT]_BBProV25fl_UnderbedOrBed](../STLs/ZBeltDrive/[HT]_BBProV25fl_UnderbedOrBed.stl) part. Flip it flat side up, insert a **M3x20 screw** into the hole in each of the 4 wings.  Spin a **M3 nut** on the bottom of each screw.



### LDO Kit Heated Bed

- Find the [[HT]_BBProV25fl_Underbed-notforbed-FOR_LDO_HEATBED](../STLs/ZBeltDrive/[HT]_BBProV25fl_Underbed-notforbed-FOR_LDO_HEATBED.stl) part. Flip it channel side up, insert a **M3x20 screw** into the hole in each of the 4 wings.  Spin a **M3 nut** on the bottom of each screw.



- Find the heatbed and heatbed thermistor from the electronics box.
- Thread the thermistor into the hole in the middle of the bottom side of the heatbed.
- Insert 3 **M3x20 screws** into the holes in the heatbed. Line up the screws to the raised posts on the [[HT]_BBProV25fl_UnderbedOrBed](../STLs/ZBeltDrive/[HT]_BBProV25fl_UnderbedOrBed.stl).  Guide the heatbed and thermistor wires along the channel before securing the two parts together with the screws and 3 **M3 nuts**.

### Fabreeko Kit Heated Bed


- Stick the **bed heater** onto the **aluminum bed** like so
  
>[!CAUTION]
>Make sure you stick the pad onto the correct side. There should be no indents around the holes for the screw heads. 



- Attach the **aluminum bed** using 3, **M3x10mm** to the [*UnderbedOrBed*](../STLs/ZBeltDrive/%5BHT%5D_BBProV25fl_UnderbedOrBed.stl) using 3, **M3 Nuts** on each screw as spacers



- The bed will fit into the base like this:



[Jump to Top](#top)

## Wiring
>[!CAUTION]
>There can be a lot of variation for running wires depending on how parts were sourced.  The most important piece is connecting the right component to the right connector on the board.

### Control Board and Axis Diagrams
This is the connection diagram for the recommended BTT SKR Mini E3 control board.  The pinout, except for the screen is the same for Marlin or Klipper and all provided configs assume this diagram is followed. 
>[!CAUTION]
>Take a moment to ensure the 3 jumpers are installed as noted on the diagram. 


In this image the Motors and Axis are labeled in color match to the pinout diagram above.


### Tub wiring

- The screen, Z axis motor, and extruder motor wires are already in the tub.  
- Connect the Z axis motor to the port labeled with the green Z.
- Connect the extruder motor to the port labeled with the pink E.
- The screen wire is going from the RS232 port on the screen to the TFT header on the board with the single wire in the bundle on the pin closest to the center of the printer.

### Toolhead wiring

- Kit builders will have an advantage during wiring as everything should be the correct length.  If self sourcing splicing, adapters, or extensions may be necessary to achieve necessary lengths.

- LDO builders have the easy way. Take the pre-made printhead cable, wrap the nylon cable sleeve around the bundle, connect the single connector end to the LDO toolboard, then feed the wires through the opening on the right side of the screen mount going through the zip tie.

- Fabreeko Kit builders will have a similar task but with separate sets of wires.

- Be sure to allow enough slack for the toolhead to move in all directions and that the cable sleeve enters into the tub to keep things neat.



- Once all the toolhead wires are in go ahead and connect them to the control board using the diagram above.  This group should include 1) Hotend Heater, 2) Hotend thermistor, 3) Hotend fan, and 4) Parts cooling fan.

>[!NOTE]
>When connecting the Bed and Hotend heaters polarity/which wires goes in which spot does not matter.

### XY wiring

- Guide the wires form the X and Y motors through the loose zip tie attached to the inside of the screen mount.



- Use a couple zip ties to join the wires together for a tidy look.

- Make sure the wire path allows for full unrestricted range of motion on the x axis and then snug up the zip tie holding the wires to the screen mount.

- Connect the X and Y motor cables to the proper ports on the control board.

- At this point everything but the heatbed heater and thermistor should be connected.  Verify the connections once more and do any cable management necessary.
>[!CAUTION]
>Try to keep all of the wires nice and low.  The belt will be just below the bottom of the curved channels on each side of the tub.  Avoid having any wires sticking up in the area to prevent them from being damaged or tangled with the belt while it moves.

### Heatbed Wiring

- The belt should still be flopped towards the back of the printer around the rear roller.

- Take the previously assembled heatbead and slid it into the inside of the belt with the square shaped wings pointing toward the rear of the printer.



- Guide the heatbed and bed thermistor wires around the side of the belt and connect them to the control board using the pinout diagram.  LDO Kit users will have a bed heater extension cable to connect as well.



[Jump to Top](#top)

## Belt and Bed

>[!NOTE]
>The Bed/Roller/Belt is a mildly tight fit, so there might be a need to stack, slide, twist or push things around a little bit.  Don't overthink the process as the roller and bed are guided to position with the belt around them.  Things should fall into place with a bit of wiggling.

- Grab the bed and move it towards the front of the printer letting the belt slide forward with it.

- Slide the second roller inside the belt and push it towards the front. Ensure the bed wires are below the roller.



- Keep moving the bed forward and slightly up while guiding the roller bearings into the slots on the frame.



- Line up the wings of the bed with the slots in the tub.



- Push the roller forward on both sides while lowering the bed fully into the slots.



- Once the bed is fully seated in the tub, on both sides push the roller forward and swing the tensioners into place cupping the bearings.



- Evenly tighten both side tensioners until the belt is nice and tight.  If the belt is too long the **M8x80 bolts** can be swapped for longer length.

- Use the screws on the 4 wings to level the bed.  This can be finely tuned during calibrations with M3 keys. The bed should be as close as possible to the height of the top of the rollers. If it is too low the print belt will be floppy and print quality will suffer.  If the bed is too tall, long prints will cause a defect or even failure when coming off the end of the belt.

## Build Complete

Congratulations!!  Your Baby Belt Pro v2 should now be completely assembled!
After you get it printing head on over to the BabyBelt Discord and request a serial number!
>[!NOTE]
>The printer below is a v2.5 LDO kit build with a couple options like filament sensor, pi, and alternative X/Y Cable routing.









[Jump to Top](#top)

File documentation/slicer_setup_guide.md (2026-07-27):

  

# BabyBelt Pro V2.5 - Slicer Setup Guide
Profiles and guidance are provided for two belt supporting slicers.  IdeaMaker and the web based Kirimoto. Ideamaker is a bit more popular however Kirimoto is completely functional for basic use.

## Orca

- See note on main [Readme](../README.md) for progress.

## IdeaMaker

## KiriMoto
>[!CAUTION]
>KiriMoto does not properly generate gcode for 30 degree printing.  The Y axis drifts down eventually crashing into the bed and running into out of range motion.  Only use this slicer when in 45 degrees.

- Grab your desired profile from our [KiriMoto Profiles folder](/Software/Profile/KiriMoto/)
- Use your browser of choice and go to https://grid.space/kiri/
- Close the greeting screen and accept that the site will use cookies. Profiles and config are stored in them.
- Click on File and select Import



- Find your downloaded .km file and select it.  You will be prompted if you would like to import the device.



- Click yes and the device selection screen will come up.  Select your newly imported device from the drop down.



- The header(start) gcode macro should look roughly like this for klipper.



- Consult the KiriMoto documentation or their discord for further information.

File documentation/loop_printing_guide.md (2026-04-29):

  

# BabyBelt Pro - Loop Printing (M808)
Marlin FW implemented what they called [M808 - Repeat Marker]([https://marlinfw.org/docs/gcode/M808.html).  The purpose of this was basically to allow belt printers that would auto unload to print multiple copies of the same thing easily.  It works like a marker system.  where you want the loop to begin you insert M808 L\<number of loops\>, then where you want the loop to end you insert M808 and that increments the loop count and goes back up to the previous M808 L line. 

For Example, the gcode below would display "Hello World" to the console 5 times.
```
M808 L5
M117 Hello World
M808
```
## Implementing loops on your Baby Belt Pro
- Marlin FW should have this functionality from 2.0.8 onward, no implementation steps should be required.
- Klipper does not natively implement M808, but it can be mimicked with a macro.
    - Make sure [loop_prints.cfg](/Software/Firmware/klipper/options/loop_prints.cfg) is in your klipper options folder.  
    - Uncomment or add [include options/loop_prints.cfg] to printer.cfg near the top with the other includes.
    - Restart klipper and check for errors.
    - In the Baby Belt Pro macros as tested in April of 2026 the L value needs to be the number of prints you want.  1 prints once, 2 prints twice etc.

## Using M808

### Manual Edit
- Open a gcode file, someplace AFTER the startup macro call insert a line M808 L\<number of loops>.  This is the starting marker for the loop.
- At the end of the gcode file BEFORE your print end macro insert a line that just has M808.  This is the end marker for the loop, when this is reached the firmware will go up to the first M808 L\<number of loops> line it sees, increment the loop count and continue.

#### Example

```
; --- startup ---
;Start GCode
PRINT_START ANGLE=45 BED=0 EXTRUDER=210 MATERIAL=0
G1 E-5.0000 F1200 ; e-retract 5
; LOOP STARTS HERE, needs to be AFTER startup macros are called.
M808 L1
G92 Z0
;; --- layer 0 (0.200 @ 0.51) ---
M106 S255
;;***Whole bunch of gcode***
G1 X46.2000 F1500
; end object id: 101
;LOOP ENDS HERE, needs to be BEFORE end macros are called
M808
;End GCode
PRINT_END
; --- filament used: 194.31 mm ---
; --- print time: 1414s ---
```
### IdeaMaker
- IdeaMaker does not have a loop field that we know of, but adding loops to start and end gcode is easy enough.
- Start Gcode

- End Gcode


### KiriMoto
- KiriMoto does have a native field for loops, but for some reason it likes to subtract one from the number of loops entered.  At some point some firmware likely treated the first pass through the loop as index 0.  The loop Count box is in the Expert section on the bottom left.  filling this in will automatically inject M808 L\<Loop Count - 1> after the startup gcode and M808 before the end gcode.
- The same results can be accomplished using the start and end gcode in the machine profile in KiriMoto as well.

- Loop Count - Add 1 to this value, the slicer will subtract one.  2 gets one print, 3 gets 2 prints etc


- Start and End Gcode - Like with IdeaMaker the L value is the number of prints/loops that will result.





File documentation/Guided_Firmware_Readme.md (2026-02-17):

<div style="text-align: center;">
  <h1>Which Firmware will you be using?</h1>
</div>

<div style="display: flex; justify-content: center; gap: 100px; margin-top: 20px;">
  <a href="Marlin/readme.md">
    Marlin
  </a>
  <a href="Klipper/readme.md">
    Klipper
  </a>
</div>

This is the guided firmware readme for the Baby Belt Pro, if you are looking for the original Baby Belt
it's [Over Here](https://github.com/RobMink/BabyBelt)

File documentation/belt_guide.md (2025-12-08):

  
# BabyBelt Pro V2 - Fabric Belt Guide
BabyBelt Pro V2 by RobMink

Jump To...

- [Tools Needed](#Tools-Needed)
- [Consumable Materials](#Consumable-Materials)
- [Prepare Fabrics](#Prepare-Fabrics)
- [Join Fabrics](#Join-Fabrics)
- [Complete](#Complete)

## Tools Needed
- Clothes Iron
- Ironing board or other heat resistant surface
- Measuring device at least 16in/400mm long
- Fabric cutter or other tool for straight accurate cuts

[Jump to Top](#top)

## Consumable Materials
- Cotton Fabric https://amzn.to/3ZorLqo - any color/pattern as long as it is cotton
- Iron-on denim backing/patch https://amzn.to/3YQTHmS
- Kapton tape https://amzn.to/43Ar142 -OR- Aluminum/HVAC Tape https://a.co/d/2Tgutt0


## Prepare Fabrics
- Take your cotton fabric out and iron it out if it needs to have any creases removed.  Give it a pull in both directions.  One way will be stretchy and one way will not be.  We want the stretchy way to be the length and the non stretchy to be width.
- Take the fabric and cut out a **5 inch (125mm) wide by 15 inch (380mm)** long strip. 
- Take the iron-on and cut out a **5 inch (125mm) wide by 15.25 inch (385mm)** long strip of iron on. An extra .25 inch (5mm) is for shrinkage and to be removed to allow for a more “seamless” design.
- The iron-on shrinks so it needs to be slightly longer. 



- If your iron-on has a backing, remove it now.



- Use the kapton tape to join the iron-on together in a loop, glue side facing out.  The tape should **ONLY** be on the glue free side of the iron-on.



- Position the fabric lengthwise in front of you with the side you want visible face down.



[Jump to Top](#top)

## Join Fabrics
**Read all steps in this section before proceeding**
- Plug-in/heat-up your iron.
    - Usually the highest non-steam setting, follow any instructions that were included with your iron-on patch.
    - How hot the belt and iron-on get will be controlled by how long the iron is held on the belt.
- Take the iron-on loop and locate the taped seam.
- Align the taped seam of the loop to the **MIDDLE** of the length of fabric.
- Ensure the fabric and iron-on are aligned on the top and bottom.
- Starting at the taped joint in the middle of the fabric strip, use the tip of the iron to heat up the iron-on and bond it to the fabric.
    - We are mostly after alignment, so no need to get the iron-on very hot leaving.  Using light heat if a mistake is made it may be able to be peeled and re-attempted.



- Verify your iron-on and fabric are still evenly aligned at the top and bottom
- Working evenly outwards from the taped seam in both directions **and** top and bottom edges, continue to use the iron to lightly heat/adhere the iron-on to the fabric.
    - Keep in mind the iron-on patch will shrink while heating.
    - Ensure even light heating, look out for the belt trying to deform into a cone or loss of alignment between the fabric and iron-on.
    - **DO NOT GO ALL THE WAY TO THE FABRIC SEAM!** Leave 1-2 inches(25-50mm) on either side of the fabric seam.



- Cut away any frayed edges from both ends of the fabric.
    - Do not trim to length, overlaps can be dealt with after the iron-on is done.
- Switch from inside the belt to folding the belt and using the iron on the fabric side.
    - Make sure you do not crease the belt while ironing on the outside.
    - Make sure the fabric and iron-on remain aligned.
    - If the fabric is too long allow it to overlap.
- Work around the entire belt, from the outside with light amounts of heat.  
    - Apply heat, pick up the belt, rotate it and continue.

This is an acceptable seam.  The belt should look something like this after the initial passes.



- The fabric and iron-on should be aligned all the way around.  Most of the shrinking of the iron-on should also be done by now.
- To deep-set the bond on the remaining passes let the iron sit a bit longer so the belt gets really hot. It should be hot enough rotating it is a bit uncomfortable.
- Keep working around the belt getting it nice and hot until it seems like it is well bonded.
    - If any edges are loose, iron it more.
    - There should be a slight darkening of the fabric while the iron-on bonds properly to the fabric.
    - It is really hard to overdo it as long as the iron is not left in one spot long enough to burn.
- Trim off any light misalignments, frayed edges, or seam overlaps.
- Make one or two more good hot passes around the entire belt after any trimming.
- Make one more pass for good measure.

## Complete
Well done, you should now have a belt ready for installation.



[Jump to Top](#top)

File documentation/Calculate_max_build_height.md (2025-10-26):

## 🧮 Solving for Max Height

**Preface:**  
The height of your bed affects the total usable build_height range of your printer.

Once your bed is leveled and your Y-offset is properly configured:

1. Temporarily increase your Y travel limit in `printer.cfg` to a higher value (e.g. `150`):
   ```
   [stepper_y]
   position_max: 150
   ```
2. Home all axes (`G28`).
3. Using **small incremental movements**, move the Y axis to its maximum safe position.
4. Record the final Y position before any mechanical limit or belt tension increase.
5. Update `[stepper_y].position_max` in your `printer.cfg` with this measured value.
6. Use the formulas below to calculate your `max_height`, and enter that value in your slicer settings.

---

### 30° Gantry

Let:  
- `C` = maximum Y travel (hypotenuse)  
- `A` = maximum vertical height  
- `B` = usable Z-axis range  

**Formula:**  
`A = C / 2`

or  
`max_height = y_max / 2`  

---

### 45° Gantry

Let:  
- `C` = maximum Y travel (hypotenuse)  
- `A` = `B` (equal vertical and horizontal components)

**Formula:**  
`A = B = C / √2`  

or  
`max_height = y_max / √2`

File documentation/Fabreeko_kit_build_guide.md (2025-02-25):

# BabyBelt Pro V2 Physical Build Guide
BabyBelt Pro V2 by RobMink

Firmware guides by TheyCallMeZ aka BlueWyvern

Physical Build Guide by Brent Lieb and Dr. Mason McNair of the Plants X Tech Lab at Michigan State University

## Introduction
Hello! This is the build guide for the BabyBelt Pro V2 by RobMink. This guide was written with new builders in mind, so don't be intimidated if this is your first printer! The guide includes images when possible and assumes the user is building from the {Fabreeko build kit w/ link?}. 

How to read this guide:
 - *Printed Parts* will be in italics
 - **Kit Parts** will be bolded
 - Printed Parts will link to the specific file in the GitHub if clicked on
 - Printed part name prefixes include
   - [a] = accent color
   - [s] = needs supports
   - [HT] = should be printed in a strong heat tolerant material (PETG, ABS, ASA, PA) to avoid premature wearing

>[!TIP] 
>If you are not familiar with 3D Printers and their components, it is recommended that you leave the parts from the kit in their packaging until the guide instructs you to unpack them. This will help you keep track of them and avoid confusion later. 
## Tools Needed 
- 2.5mm Hexagonal Screwdriver
- 2mm Hexagonal Screwdriver
- 1.5mm Hexagonal Screwdriver
- Adjustable Wrench
- Wire Cutters
- Small Flathead Screwdriver
- Files (Good to have on hand if any parts print with slight imperfections)
- Scissors & Iron (For print belt)

## Printed Parts
### Printing Parts
Most of the parts of this kit can be printed out of normal PLA, allowing for a wide range of colors and stylistic choices! The parts that shouldn't be printed out of PLA are listed below. 

- [*NEMA17_ZGear*](../STLs/ZBeltDrive/[a]_BBProV25fl_Nema17_ZGear.stl)
- [*Roller_ZGear*](../STLs/ZBeltDrive/[a]_BBProV25fl_Roller_ZGear.stl)
- [*UnderbedOrBed*](../STLs/ZBeltDrive/[HT]_BBProV25fl_UnderbedOrBed.stl)

We recommend printing all parts with standard Voron style settings:

- Layer height: 0.2mm
- Extrusion width: 0.4mm, forced
- Infill percentage: 40%
- Infill type: grid, gyroid, honeycomb, triangle, or cubic
- Wall count: 4
- Solid top/bottom layers: 5

The design inspiration for the printer built for this guide was to make a printer out of "wood", "stone", and "glass" which is why we selected [Timberfill](https://fillamentum.com/collections/timberfill-filament/) as the primary filament, [Marble PLA](https://us.polymaker.com/products/panchroma-marble?variant=43612877946937) for the accent color, and [Fiberon PA6-GF](https://us.polymaker.com/products/fiberon-pa6-gf25) for the heat tolerant components. 

### Part List

Coming Soon!

>[!NOTE]
>If you are using a Revo-style Hot End and not the Bamboo nozzle that comes with the Fabreeko kit, then the gantry-carriage parts will be slightly different and can be found in the "Mods" folder.

## Kit Parts
This is what the box will look like when you receive it.  

 

This is all the parts that will be inside the box, spread out for visibility.  

Baby Belt Kit Parts

### Part List

Coming Soon! In the meantime [see the BOM here](https://docs.google.com/spreadsheets/d/19PbR3nFbQ4-eIOTU0kmoTl5-mHv_KsTnUdfFXekWg-I/edit?gid=0#gid=0)

## Physical Build
>[!NOTE]
>There are several times during this build when a component will be secured with multiple screws. It is generally recommended to NOT fully tighten a screw before the rest have been started, to make sure parts line up correctly and don't crack. 
### Base
> I mean I prefer treble but okay

Start by constructing the base. 
- Place an **M3 Nut** into the hole indicated by the arrow in [*Side-B*](../STLs/Frame/BBProV25fl_Side-B.stl)


- Join the two sides together and place one **M3x20 screw** into the indicated hole in [*Side-A*](../STLs/Frame/BBProV25fl_Side-A.stl) and tighten. 


The base should now look like this.



### Power Switch and Jack
> Who's Jack? I don't know any Jack

Next install the **power jack** and **switch**. 



- There are two circular holes next to each other on [*Side-B*](../STLs/Frame/BBProV25fl_Side-B.stl) of the printer. 
- The black rubber cover for the power jack is optional
- Secure the power jack with the supplied nut
- The power switch will lock into place once pushed in
  


Here is what it should look like from the other side. 



- Wire the two components as such
- Wrap in electrical tape or use heat-shrink tubing (not supplied) to insulate the connections and avoid accidental shorting
- We opted to solder the wires to the connectors for this build



### Board
> All aboard!

- Install the SKR board by the power switch using 3, **M3x10mm**



- Make sure the Micro-USB and MicroSD ports line up with the holes for them in the side panel



- Connect the wires from the power switch & power jack to the SKR board as shown below




### Screen
> AAAAAAAAAAAHHHHHHHHH, oh sorry I thought you said scream

Next we will install the screen.



- Use 4, **M3x10mm** to connect the screen to the [*Screenmount*](../STLs/Frame/%5Bs%5D_BBProV24fl_Screenmount.stl)



Here is what it should look like. 



- Attach the knob by pushing it onto the silver dial beneath the screen





- Plug the wire into the port labeled RS232 on the back of the screen using the black plastic connector that combines all the wires into one





- Attach the [*screen mount*](../STLs/Frame/%5Bs%5D_BBProV24fl_Screenmount.stl) to the frame by inserting one **M3 Nut** into the hole on the bottom of the frame, next to where it slots into the base 



- Insert one **M3x20mm** into the hole on the side of the frame and use it to secure the [*screen mount*](../STLs/Frame/%5Bs%5D_BBProV24fl_Screenmount.stl)



Next use 2, **M3x10mm screws** and 2, **M3 Nuts** to attach the screen mount with the two holes in the top. 





Tada! You have installed the screen!

### Extruder
> I barely know 'er!
- Attach the **gear** to the **NEMA 17 stepper motor** ensuring that the **grub screw** is tight against the flat part of the motor shaft
>[!NOTE]
> Make sure the gear fits properly with the rest of the gears in the extruder



- Line up the motor with the mounting holes in the side of the frame



- Attach the extruder to the outside of the frame with 4, **M3x10mm** screws



### Belt Tensioner
> Consider loosening or removing after big holiday meals

Next we will build and install the belt tensioners. 
>[!NOTE]
>There are two of these, so do each step twice.



- Fit a **M8 Nut** into [*PrintBelt_Pusher-A*](../STLs/PrintBelt/%5Ba%5D_BBProV25fl_PrintBelt-Pusher-A.stl)/[*PrintBelt_Pusher-B*](../STLs/PrintBelt/%5Ba%5D_BBProV25fl_PrintBelt-Pusher-B.stl)
- Secure it with a **M8x70mm** Screw 




- Fit another **M8 Nut** into the [*PrintBelt_Nut*](../STLs/PrintBelt/%5Ba%5D_BBProV25fl_PrintBelt-Nut(2x).stl) and line up with the hole on the [*PrintBelt_Frame-A*](../STLs/PrintBelt/%5Ba%5D_BBProV25fl_PrintBelt-Frame-A.stl)/[*PrintBelt_Frame-B*](../STLs/PrintBelt/%5Ba%5D_BBProV25fl_PrintBelt-Frame-B.stl).




Congratulations! You have built your tensioners! They should look like this.



- There are spots for the tensioners to fit on either side of the base. 



- Use a **M3x20mm screw** to install both of the tensioners with the curved portion facing downward. 




### Rollers
> Not the kind your grandma used to wear

- Wrap both [*rollers*](../STLs/ZBeltDrive/%5Ba%2Cs%5D_BBProV25fl_Roller%5Bx2%5D.stl) in electrical tape to maintain a better grip on the belt
- We recommend 2 wraps, with the 2nd one helping to hold the first in place 
- Place a **M8 Nut** into the side slot and then inserting a **M8x70 Hex Screw** with a **608ZZ bearing** fully into the [*roller*](../STLs/ZBeltDrive/%5Ba%2Cs%5D_BBProV25fl_Roller%5Bx2%5D.stl)






- On one of the rollers, install the [*Roller_ZGear*](../STLs/ZBeltDrive/%5Ba%5D_BBProV25fl_Roller_ZGear.stl) on the screw, before the bearing




### Print Belt
> Personally I prefer leopard

Follow the guide below to make the printbelt. <br>
https://docs.google.com/document/d/13pu9LH_nKmDJY-V2nZXMY8CHur7INB6-9V5sKlAuCuE/edit?usp=sharing

### Z Motor
> Which one? OOOOHHHH you mean like the axis



- Attach the Z motor to the frame using 4, **M3x10mm screws** 



- Make sure the wire port on the motor is facing towards the screen 



- Install the [*NEMA 17_Z Gear*](../STLs/ZBeltDrive/%5Ba%5D_BBProV25fl_Nema17_ZGear.stl) onto the motor and then check to make sure it lines up with the gear on the [*Roller_ZGear*](../STLs/ZBeltDrive/%5Ba%5D_BBProV25fl_Roller_ZGear.stl) we installed on one of the rollers earlier




Improperly fitting vs Properly fitting gears




- Place a **M3 Nut** into the slot on the side of the frame right above the motor. Repeat on the other side




- Use a **M3 Nut** and **M3x20mm** screw to attach the [*scraper*](../STLs/Frame/BBProV25fl_scraper.stl) in the same manner the screen mount was attached previously
- Use a **M3x10mm** to attach the scraper below the roller, securing into the nuts we previously inserted 




>[!NOTE]
>To complete this guide, we decided to leave the belt off during this step to make it easier to get clear images of the build as it progressed. Even once the printer is built, removing the scraper and replacing the belt is quick and easy. At this point, we suggest you install the Z roller with the belt so it looks like the picture on the right. 




### Y Stop
> Because we said so

- Insert the [*TensionIdlerHolder*](../STLs/Gantry/Y/%5Ba%5D_BBProV25fl_RockMonsterNo1YTentionerIdlerHolder.stl) into the [*TensionBody*](../STLs/Gantry/Y/%5Ba%5D_BBProV25fl_RockMonsterNo1YTentionerBody.stl) with the larger hole (to accommodate for the screw head) on the same side as the circular indentation on the body
- Make sure your orientation matches the following pictures
- Keep the [*TensionIdlerHolder*](../STLs/Gantry/Y/%5Ba%5D_BBProV25fl_RockMonsterNo1YTentionerIdlerHolder.stl)  in place with a **M3x20mm screw**




>[!CAUTION]
>Make sure the configuration of your [*TensionIdlerHolder*](../STLs/Gantry/Y/%5Ba%5D_BBProV25fl_RockMonsterNo1YTentionerIdlerHolder.stl)  and [*TensionBody*](../STLs/Gantry/Y/%5Ba%5D_BBProV25fl_RockMonsterNo1YTentionerBody.stl) are correct before proceeding.

### Hotend Fan
> For the printer not you ;)

Attach the [*YCar_Bam_Fan*](../STLs/Gantry/Carriage/Bambu/%5Ba%5D_BBProV25fl_YCar_Bam_Fan.stl) to the [*YCar_Bam_BeltHolder*](../STLs/Gantry/Carriage/Bambu/%5Ba%5D_BBProV25fl_YCar_Bam_BeltHolder.stl) by inserting 2, **M3x10 screws** into the holes indicated in the first image, and through the whole in the second image
- Secure with **M3 Nuts** 




Your part should now look like this. 



- Orient the fan so that the air flow will move towards the air duct on the fan mount, then secure where indicated with zip ties 


- Use a zip tie to secure the wires to the side of the carriage 

### Y Gantry
> well it sounds better than support, platform, or bracket

- Insert a **M3 Nut** into this slot on the [*YCar_Bam_Side-A*](../STLs/Gantry/Carriage/Bambu/%5Ba%5D_BBProV25fl_YCar_Bam_SideA.stl)

>[!CAUTION]
> We highly recommend lubricating **all** the linear rail bearings (visible in the photo below) using something like Mobil EP1 or EP2 grease prior to installation. Nero3D has a [great guide providing explanations and how-tos for this](https://youtu.be/UYvhYjkBFTY?si=frlAKNLAvElEVHFv) 



- Attach the carriage to the **linear rail** using 4, **M2x6mm screws**



- Insert a **M3 Nut** into the still exposed slot on the [*YCar_Bam_Side-A*](../STLs/Gantry/Carriage/Bambu/%5Ba%5D_BBProV25fl_YCar_Bam_SideA.stl)




- It should line up with the hotend fan like so:



- Insert **M3 Nuts** into the slots indicated on the [*YCar_Bam_Side-B*](../STLs/Gantry/Carriage/Bambu/%5Ba%5D_BBProV25fl_YCar_Bam_SideB.stl)


 

Next we will install the hotend to the [*YCar_Bam_Side-B*](../STLs/Gantry/Carriage/Bambu/%5Ba%5D_BBProV25fl_YCar_Bam_SideB.stl)



- Use a **M3x20mm screw** and a **M3 Nut** to attach the hotend to the [*YCar_Bam_Side-B*](../STLs/Gantry/Carriage/Bambu/%5Ba%5D_BBProV25fl_YCar_Bam_SideB.stl)
through the hole shown at the top




- Make sure the screw goes through the correct hole on the hotend



- Insert **M3 Nuts** into the holes pictured 

 
 


- Attach the hotend fan assembly to the rail carriage (this is easier to do one half at a time)
- Use **M3x8mm screws** for the top holes and **M3x10mm screws** for the holes nearest the nozzle. 

 
 
 


### Hotend
> Again talking about the printer, not yours

Next we will install the electrical components to the hotend. 



- Insert the **thermistor** into the small hole in the block right above the nozzle



The thermistor



- Run the wire through the channel built into the black **heat break**. 



- Place the **heater cartridge** on the front of the block and run the wires through the same channel as the thermistor
- Secure it and the thermistor in place with the **metal clip** 



### Parts Fan
> Not to be confused with a whole fan. I mean it is a whole fan, but it's for cooling parts.

Time to install the **part cooling fan** to the front of the **hotend heatbreak**. 



- Insert **M3 nuts** into these slots of the current assembly 



- Using 2, **M3x20mm screws** on top and 2, **M2.5x12mm** screws on bottom to secure the hotend fan




### X Gantry
> The breakup was hard on everyone

- Line up the **smooth idlers** with the indicated holes and secure in place with 2, **M3x20 screws**



- Your gantry should now look like this. The yellow boxes indicate where the gantry will be attached to the pair of **linear rails**
- Attach the gantry to the linear rails using 8 **M2x6 screws** (4 for each linear rail) 




>[!CAUTION]
> Last chance to lubricate the remaining linear rails!

Here's what it should look like with the rails attached. 



>[!Note]
>Unfortunately, we missed taking photos installing the [*X_RailMount_Side-A*](../STLs/Gantry/X/%5Ba%5D_BBProV25fl_XrailMount-SideA.stl) and [*X_RailMount_Side-B*](../STLs/Gantry/X/%5Ba%5D_BBProV25fl_XrailMount-SideB.stl)
>Attach these printed parts using 4, **M2x8mm screws** and 4, **M2 Nuts**





### Combining Axes
> FUSION HA!
> 



- Attach the linear rail of the Y axis to the X gantry as shown below, using 2, **M2x8mm screws** and 2, **M2 Nuts**



- Attach the [*LinearRailReplacement*](../STLs/Gantry/Y/BBProV25fl_LinearRailReplacement.stl) on the other side of the Y axis in the same way 




### GT2 Belts
> Gran Turismo 2 was the best one, not sure why people keep bringing up belts tho...

>[!NOTE]
>When installing the GT2 belts, try to get them as tight as possible when you first install them. This will make it easier to get the right tension later. You can pre-cut the belts to 480mm (Y axis) and 290mm (X axis) and trim down when finishing, or you can run a much longer length (even the full uncut belt) to make sure you don't cut your belt too short. Either way you will have some leftover. 
 
- Run the belt through the Y stop, teeth facing toward the idler, and secure the first 3 teeth into the Y gantry





Next install the **Y motor** onto the X gantry. 



- Install the **pulley** onto the motor shaft, making sure the **grub screw** is on the flat face of the shaft




- Install the motor onto the X gantry in the position that is closest to the hotend using 4, **M2.5x8mm** screws




- Run the belt through the X gantry and around the pulley



- Cut the belt so that it fits into the remaining teeth and secure in place with a zip tie




>[!Caution]
>The printed parts shown for the X axis belt attachment steps are not the most current up-to-date versions, we will update the photos when we can. The main difference is that instead of mounting the GT2 belt directly to the X_RailMount_Side-A & X_RailMount_Side-B like in our instructions below you will attach the belt using the [*X_PivotArm*](../STLs/Gantry/X/%5Ba%5D_BBProV25fl_pivotArm(2x).stl) and [*X_Pivot Clamp*](../STLs/Gantry/X/%5Ba%5D_BBProV25fl_XPivotClamp(2x).stl)
>

- Run the belt for the X Axis as seen below, going through the lower hole on the right



- Loop the belt around the outside, through the second hole, and then interlock the teeth and pull till it is firmly locked into the first hole (this can be a bit tricky and may take several tries to get it just right) 



- Push the belt to make space for the pulley on the X axis motor (prepared identically to the Y axis motor)




- Attach the X belt tensioner on the left side of the assembly using a **M3x20 screw** 



- Run the belt through the bottom slot and then through the top slot and secure with a zip tie




- Insert a **M3x10mm screw** and **M3 Nut** to the hole in the top of the tensioner. This can be used to adjust the belt tension as needed. 





### Heated Bed
> For those cold winter nights



- Stick the **bed heater** onto the **aluminum bed** like so
  
>[!CAUTION]
>Make sure you stick the pad onto the correct side. There should be no indents around the holes for the screw heads. 



- Attach the **aluminum bed** using 3, **M3x10mm** to the [*UnderbedOrBed*](../STLs/ZBeltDrive/%5BHT%5D_BBProV25fl_UnderbedOrBed.stl) using 3, **M3 Nuts** on each screw as spacers



- The bed will fit into the base like this:



### Wiring
> It's electric, Boogie woogie, woogie! Well, not yet but soon^TM^.

Let's get those wires connected!

>[!NOTE]
>This hole located on the right of the screen holder is where all wires from the outside of the base should be routed through. This includes the X and Y motors, both fans, the thermistor, and heater. <br>
>

>[!TIP]
>Wire management can be difficult and can take some practice to get good at. The most important thing is making sure the wires are easily identifiable and are not in the way of any moving components. 

- Start by plugging in the motors
- There are 5 (slots) on the side of the board closest to the screen 



- From left to right is the X motor, Y motor, Z motor, and Extruder. At this time you should also install the 3 red jumpers pictured in the bottom right



- Plug both fans in. ***NOTE:*** *The wires in our kit were a bit short, and we had to extend them. This is now fixed in the kits so your wire colors likely will not match the photos.* The hotend fan is shown with blue and green wires, while the parts fan is shown with red and black 



- Install the heater cartridge wires into the screw terminal located right next to them (orientation is not important)



- Both thermistors are plugged in on the opposite side of the board. ***NOTE:*** *The wires in our kit were a bit short, and we had to extend them. This is now fixed in the kits so your wire colors likely will not match the photos.* The hotend thermistor is shown with blue and green wires, while the bed thermistor has red and black. 



- The bed heater wires can be installed in the screw terminal next to where we installed the hotend (orientation does not matter)



- Plug the screen wires into the freestanding pins located above the jumpers 



### Print Belt
> The end of the road! I mean technically it's a loop so there is no end

Now that all the insides are done we can do final assembly of the belt. This is straightforward, but can be a bit tricky to make everything fit right. If things aren't fitting right or moving smoothly DO NOT force anything, try sanding at any pain points and try again.



- Place the heatbed inside the belt, with the plastic prongs facing upwards and slot them into the frame



- Slide the other roller into the belt and maneuver it into the curved slots in the frame
- Use the belt tensioners to get the belt tensioned just right



### Finished Printer
- Attach the bowden tube from the extruder to the hotend and you have finished the physical build of your printer!



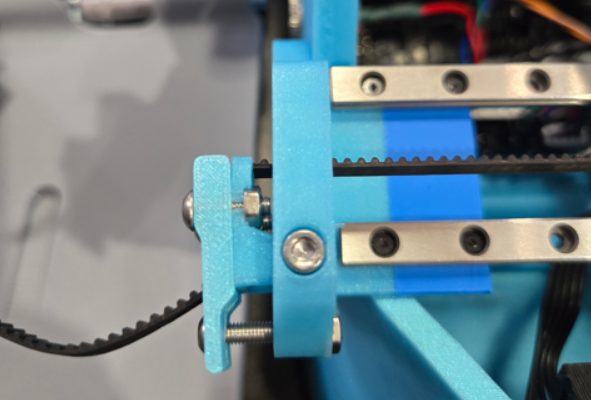
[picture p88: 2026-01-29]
documentation/images/build_guide/x-axis-9.png

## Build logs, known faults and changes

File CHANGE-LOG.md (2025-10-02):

# Change Log

### 2025-09-29  
- Added a markdown printer parts list similar to the old google doc

### 2025-08-25  

- Created this new fancy pants Change log! (and linked to it from the readme)
- Updated Bed/Underbed to the latest model field tested at RMRRF! Now with better adjustability and cable routing!  
    - 3x M3X16 SHCS should be used to have no threads produting from the underbed.
    - 4x M3x20 SHCS - For Bed height adjustment
    - 7x M3 Nut
    - If for some reason you still need / want to use the old one you can download it [Here](https://github.com/RobMink/BabyBeltPro/blob/938c1f90842c4cdaf9e164276722ffa35ede7eaa/STLs/ZBeltDrive/%5BHT%5D_BBProV25fl_UnderbedOrBed.stl)
- Added **\*NEW\*** folder where applicable for 3MF Files for MMU Painted and/or AMS painted files (We will slowly be adding these over time)
- Formatted README.MD to be cleaner
- Added the "Printcepts Ethos" (Our Guiding principles)
- Added Links to Belt Slicers in Readme
- Added LDO Kit Marlin Firmware
- Added LDO Kit Toolhead Board Mount stl

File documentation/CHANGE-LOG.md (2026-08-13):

# Change Log

## 2026-08-13
 - Updated X Motor mount with extra lift (avoids stepper shaft hitting the carrier)
 - Build Guide updates - Thank you Nero!
 - Printed Parts list updates
    - Took off EACS toolhead parts, LDO 2.6 kits ship with a couple instead of EACS fittings..YAY!
    - Added image and notes for the two bed types (heated bed and printed bed)

## 2026-06-25
 - Added links to OrcaSlicer Nightly w/ belt support
 - Added note to build guide to chase heatsinks with an M3/20

## 2026-06-20
 - BabyBeltPro v2.6
    - Changed from 3 MGN7H rails (2X 1Y) to 1 MGN9C(Y) and 1 MGN12C(X)
    - Removed 2mm screws (2.5s still needed for steppers and some hotend parts)
    - Added M3x6 BHCS (Y Gantry to MGN12 rail) and M3x30 SHCS (new X gantry to frame)
    - enhanced X gantry components for increased stability
        - X gantry now uses heatsets M3x4x5 (Voron style)
        - Backwards compatible with 2.5 BOM rails (mgn7H)
    - Improved hole and screw insertion patterns for easier installation on Y axis
    - Revised X/Y stepper mounting for easier install/maintenance
 - Added 2.6 and 2.6 to 2.5 diff BOM links
 - Updated build guide for 2.6 

## 2026-04-28
 - New profile for klipper FW and KiriMoto Slicer
 - Updated y-axis macros to include a -/+ 1mm move (community request)
 - New optional config to enable loop printing (M808)
 - Add M808/loop printing guide
 - New optional config to mask bed heater commands
 - New Slicer setup guide with KiriMoto instructions
 - Update main docs readme
 - Fix typo in build guide

## 2026-01-29
 - Documentation revamp
    - Added a Documentation Index to clean up main readme
    - Updated printed parts guide with roller recommendations
    - Removed print settings recommendations from anywhere outside of the printed parts guide.  If you find any let us know.
    - Added a new markdown format build guide.  This is a combination of the older Google Doc, the fabreeko kit guide, and community contributed updates based on the LDO kit
    - Added link to LDO/West3D Kit
    - Fixed printcepts page link
    - Ran a spell checker against new docs

### 2025-09-29  
- Added a markdown printer parts list similar to the old google doc

### 2025-08-25  

- Created this new fancy pants Change log! (and linked to it from the readme)
- Updated Bed/Underbed to the latest model field tested at RMRRF! Now with better adjustability and cable routing!  
    - 3x M3X16 SHCS should be used to have no threads protruding from the underbed.
    - 4x M3x20 SHCS - For Bed height adjustment
    - 7x M3 Nut
    - If for some reason you still need / want to use the old one you can download it [Here](https://github.com/RobMink/BabyBeltPro/blob/938c1f90842c4cdaf9e164276722ffa35ede7eaa/STLs/ZBeltDrive/%5BHT%5D_BBProV25fl_UnderbedOrBed.stl)
- Added **\*NEW\*** folder where applicable for 3MF Files for MMU Painted and/or AMS painted files (We will slowly be adding these over time)
- Formatted README.MD to be cleaner
- Added the "Printcepts Ethos" (Our Guiding principles)
- Added Links to Belt Slicers in Readme
- Added LDO Kit Marlin Firmware
- Added LDO Kit Toolhead Board Mount stl

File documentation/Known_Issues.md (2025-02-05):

# This page is for issues that we have discovered and potential workarounds if available. 

- [Motors Turn in the Wrong Direction](#motors-turn-in-the-wrong-direction)  
- [Motors Won't turn in either direction](#motors-wont-turn-in-either-direction)  
- [KlipperScreen Issues](#klipperscreen-issues)  
- [Bambu Nozzle can't touch the Bed](#bambu-nozzle-cant-touch-the-bed)
- [External Resources](#external-resources)

## Motors Turn in the wrong direction

Klipper Solution:

```markdown
    Edit your printer.cfg on the machine and find the axis that is moving in the wrong direction 
    [stepper_x], [stepper_y], [stepper_z], [extruder]
    find the dir_pin: entry 
    If there is a ! remove it, if there is not a ! add it to the front of the pin assignment. This tells the Klipper firmware to invert the direction based on how the wires are run.
    !PC1 => PC1
    PC1 => !PC1  
```

Marlin Solution:

```markdown
    This is slightly trickier because it requires changing the physical pin order on your cable or recompiling the firmware
    If you are comfortable recompiling find the line in question that says
        #define INVERT_<axis>_DIR false (or true)
    and change its value
        #define INVERT_X_DIR true => #define INVERT_X_DIR false

    If you are not comfortable recompiling firmware, you can change the direction of your motor by changing it's wiring order. 
    Please refer to the documentation of your stepper motor to ensure you are performing this step correctly. 
    
    (De-pin/Re-pin the end that plugs into your board)
    If you are unsure how, please check the External Resources section for the Re-Pin JST Video
    If your motor is wired as such
    A1 A2 B1 B2
    Then simply swap A1 and A2 so it is wired as
    B2 B1 A2 A1
    and the motor direction will change.
```

## Motors won't turn in either direction

```markdown
    Your Coil wires are mixed up my dude.... 
    When referencing your motor's documentation they probably look something like this
    A1 B1 A2 B2
    Coil pairs need to be together like this
    A1 A2 B1 B2
```

## KlipperScreen Issues

### Emergency Stop on Left Menu Instead of Power Options while not printing  
This is an issue that has been found when using a pre-built image where Klipper / KlipperScreen / etc has been pre-installed. The solution is simply to install [KIAUH](https://github.com/dw-0/kiauh) and use it to remove and re-install KlipperScreen with the default options. 

## Bambu Nozzle Can't Touch the Bed
Super simple solution here, take the sock off. 

## External Resources
[Re-Pin JST YouTube Video](https://www.youtube.com/watch?v=JPkvHr-mIdc)

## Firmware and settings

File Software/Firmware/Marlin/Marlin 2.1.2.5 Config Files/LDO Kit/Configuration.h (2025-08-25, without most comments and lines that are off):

#pragma once
#define CONFIGURATION_H_VERSION 02010205
#define STRING_CONFIG_H_AUTHOR "Printcepts BBPro A" // Who made the changes.
#define SHOW_BOOTSCREEN
  #define MOTHERBOARD BOARD_BTT_SKR_MINI_E3_V3_0
#define SERIAL_PORT 2
#define BAUDRATE 115200
#define BAUD_RATE_GCODE     // Enable G-code M575 to set the baud rate
#define SERIAL_PORT_2 -1
#define BAUDRATE_2 115200   // :[2400, 9600, 19200, 38400, 57600, 115200, 250000, 500000, 1000000] Enable to override BAUDRATE
#define CUSTOM_MACHINE_NAME "BabyBelt Pro-LDO"
#define X_DRIVER_TYPE  TMC2209
#define Y_DRIVER_TYPE  TMC2209
#define Z_DRIVER_TYPE  TMC2209
#define E0_DRIVER_TYPE TMC2209
#define EXTRUDERS 1
#define DEFAULT_NOMINAL_FILAMENT_DIA 1.75
#define TEMP_SENSOR_0 5
#define TEMP_SENSOR_1 0
#define TEMP_SENSOR_2 0
#define TEMP_SENSOR_3 0
#define TEMP_SENSOR_4 0
#define TEMP_SENSOR_5 0
#define TEMP_SENSOR_6 0
#define TEMP_SENSOR_7 0
#define TEMP_SENSOR_BED 1
#define TEMP_SENSOR_PROBE 0
#define TEMP_SENSOR_CHAMBER 0
#define TEMP_SENSOR_COOLER 0
#define TEMP_SENSOR_BOARD 0
#define TEMP_SENSOR_REDUNDANT 0
#define DUMMY_THERMISTOR_998_VALUE  25
#define DUMMY_THERMISTOR_999_VALUE 100
#if TEMP_SENSOR_IS_MAX_TC(0)
  #define MAX31865_SENSOR_OHMS_0      100 // (Ω) Typically 100 or 1000 (PT100 or PT1000)
  #define MAX31865_CALIBRATION_OHMS_0 430 // (Ω) Typically 430 for Adafruit PT100; 4300 for Adafruit PT1000
#endif
#if TEMP_SENSOR_IS_MAX_TC(1)
  #define MAX31865_SENSOR_OHMS_1      100
  #define MAX31865_CALIBRATION_OHMS_1 430
#endif
#if TEMP_SENSOR_IS_MAX_TC(2)
  #define MAX31865_SENSOR_OHMS_2      100
  #define MAX31865_CALIBRATION_OHMS_2 430
#endif
#if HAS_E_TEMP_SENSOR
  #define TEMP_RESIDENCY_TIME         10  // (seconds) Time to wait for hotend to "settle" in M109
  #define TEMP_WINDOW                  1  // (°C) Temperature proximity for the "temperature reached" timer
  #define TEMP_HYSTERESIS              3  // (°C) Temperature proximity considered "close enough" to the target
#endif
#if TEMP_SENSOR_BED
  #define TEMP_BED_RESIDENCY_TIME     10  // (seconds) Time to wait for bed to "settle" in M190
  #define TEMP_BED_WINDOW              1  // (°C) Temperature proximity for the "temperature reached" timer
  #define TEMP_BED_HYSTERESIS          3  // (°C) Temperature proximity considered "close enough" to the target
#endif
#if TEMP_SENSOR_CHAMBER
  #define TEMP_CHAMBER_RESIDENCY_TIME 10  // (seconds) Time to wait for chamber to "settle" in M191
  #define TEMP_CHAMBER_WINDOW          1  // (°C) Temperature proximity for the "temperature reached" timer
  #define TEMP_CHAMBER_HYSTERESIS      3  // (°C) Temperature proximity considered "close enough" to the target
#endif
#if TEMP_SENSOR_REDUNDANT
  #define TEMP_SENSOR_REDUNDANT_SOURCE    E1  // The sensor that will provide the redundant reading.
  #define TEMP_SENSOR_REDUNDANT_TARGET    E0  // The sensor that we are providing a redundant reading for.
  #define TEMP_SENSOR_REDUNDANT_MAX_DIFF  10  // (°C) Temperature difference that will trigger a print abort.
#endif
#define HEATER_0_MINTEMP   5
#define HEATER_1_MINTEMP   5
#define HEATER_2_MINTEMP   5
#define HEATER_3_MINTEMP   5
#define HEATER_4_MINTEMP   5
#define HEATER_5_MINTEMP   5
#define HEATER_6_MINTEMP   5
#define HEATER_7_MINTEMP   5
#define BED_MINTEMP        5
#define CHAMBER_MINTEMP    5
#define HEATER_0_MAXTEMP 275
#define HEATER_1_MAXTEMP 275
#define HEATER_2_MAXTEMP 275
#define HEATER_3_MAXTEMP 275
#define HEATER_4_MAXTEMP 275
#define HEATER_5_MAXTEMP 275
#define HEATER_6_MAXTEMP 275
#define HEATER_7_MAXTEMP 275
#define BED_MAXTEMP      150
#define CHAMBER_MAXTEMP  60
#define HOTEND_OVERSHOOT 15   // (°C) Forbid temperatures over MAXTEMP - OVERSHOOT
#define BED_OVERSHOOT    10   // (°C) Forbid temperatures over MAXTEMP - OVERSHOOT
#define COOLER_OVERSHOOT  2   // (°C) Forbid temperatures closer than OVERSHOOT
#define PIDTEMP           // See the PID Tuning Guide at https://reprap.org/wiki/PID_Tuning
#define PID_MAX  255      // Limit hotend current while PID is active (see PID_FUNCTIONAL_RANGE below); 255=full current
#define PID_K1     0.95   // Smoothing factor within any PID loop
    #define DEFAULT_Kp  22.20
    #define DEFAULT_Ki   1.08
    #define DEFAULT_Kd 114.00
#define MAX_BED_POWER 255 // limits duty cycle to bed; 255=full current
#define MAX_CHAMBER_POWER 255 // limits duty cycle to chamber heater; 255=full current
  #define PID_FUNCTIONAL_RANGE 10 // If the temperature difference between the target temperature and the actual temperature
#define PREVENT_COLD_EXTRUSION
#define EXTRUDE_MINTEMP 170
#define PREVENT_LENGTHY_EXTRUDE
#define EXTRUDE_MAXLENGTH 500
#define THERMAL_PROTECTION_HOTENDS // Enable thermal protection for all extruders
#define THERMAL_PROTECTION_BED     // Enable thermal protection for the heated bed
#define THERMAL_PROTECTION_CHAMBER // Enable thermal protection for the heated chamber
#define THERMAL_PROTECTION_COOLER  // Enable thermal protection for the laser cooling
#define USE_XMIN_PLUG
#define USE_YMIN_PLUG
#define USE_ZMIN_PLUG
#define ENDSTOPPULLUPS
#define X_MIN_ENDSTOP_INVERTING false // Set to true to invert the logic of the endstop.
#define Y_MIN_ENDSTOP_INVERTING false // Set to true to invert the logic of the endstop.
#define Z_MIN_ENDSTOP_INVERTING false // Set to true to invert the logic of the endstop.
#define I_MIN_ENDSTOP_INVERTING false // Set to true to invert the logic of the endstop.
#define J_MIN_ENDSTOP_INVERTING false // Set to true to invert the logic of the endstop.
#define K_MIN_ENDSTOP_INVERTING false // Set to true to invert the logic of the endstop.
#define U_MIN_ENDSTOP_INVERTING false // Set to true to invert the logic of the endstop.
#define V_MIN_ENDSTOP_INVERTING false // Set to true to invert the logic of the endstop.
#define W_MIN_ENDSTOP_INVERTING false // Set to true to invert the logic of the endstop.
#define X_MAX_ENDSTOP_INVERTING false // Set to true to invert the logic of the endstop.
#define Y_MAX_ENDSTOP_INVERTING false // Set to true to invert the logic of the endstop.
#define Z_MAX_ENDSTOP_INVERTING false // Set to true to invert the logic of the endstop.
#define I_MAX_ENDSTOP_INVERTING false // Set to true to invert the logic of the endstop.
#define J_MAX_ENDSTOP_INVERTING false // Set to true to invert the logic of the endstop.
#define K_MAX_ENDSTOP_INVERTING false // Set to true to invert the logic of the endstop.
#define U_MAX_ENDSTOP_INVERTING false // Set to true to invert the logic of the endstop.
#define V_MAX_ENDSTOP_INVERTING false // Set to true to invert the logic of the endstop.
#define W_MAX_ENDSTOP_INVERTING false // Set to true to invert the logic of the endstop.
#define Z_MIN_PROBE_ENDSTOP_INVERTING false // Set to true to invert the logic of the probe.
#define DEFAULT_AXIS_STEPS_PER_UNIT   { 100, 100, 364, 410 }
#define DEFAULT_MAX_FEEDRATE          { 70, 70, 10, 30 }
#define DEFAULT_MAX_ACCELERATION      { 1250, 900, 75, 1500 }
#define DEFAULT_ACCELERATION          3000    // X, Y, Z and E acceleration for printing moves
#define DEFAULT_RETRACT_ACCELERATION  3000    // E acceleration for retracts
#define DEFAULT_TRAVEL_ACCELERATION   3000    // X, Y, Z acceleration for travel (non printing) moves
#define DEFAULT_EJERK    5.0  // May be used by Linear Advance
  #define JUNCTION_DEVIATION_MM 0.013 // (mm) Distance from real junction edge
  #define JD_HANDLE_SMALL_SEGMENTS    // Use curvature estimation instead of just the junction angle
#define NOZZLE_TO_PROBE_OFFSET { 10, 10, 0 }
#define PROBING_MARGIN 10
#define XY_PROBE_FEEDRATE (133*60)
#define Z_PROBE_FEEDRATE_FAST (4*60)
#define Z_PROBE_FEEDRATE_SLOW (Z_PROBE_FEEDRATE_FAST / 2)
#define Z_CLEARANCE_DEPLOY_PROBE   10 // (mm) Z Clearance for Deploy/Stow
#define Z_CLEARANCE_BETWEEN_PROBES  5 // (mm) Z Clearance between probe points
#define Z_CLEARANCE_MULTI_PROBE     5 // (mm) Z Clearance between multiple probes
#define Z_PROBE_LOW_POINT          -2 // (mm) Farthest distance below the trigger-point to go before stopping
#define Z_PROBE_OFFSET_RANGE_MIN -20
#define Z_PROBE_OFFSET_RANGE_MAX 20
#define X_ENABLE_ON 0
#define Y_ENABLE_ON 0
#define Z_ENABLE_ON 0
#define E_ENABLE_ON 0 // For all extruders
#define DISABLE_OTHER_EXTRUDERS   // Keep only the active extruder enabled
#define INVERT_X_DIR true
#define INVERT_Y_DIR true
#define INVERT_Z_DIR true
#define INVERT_E0_DIR true
#define INVERT_E1_DIR false
#define INVERT_E2_DIR false
#define INVERT_E3_DIR false
#define INVERT_E4_DIR false
#define INVERT_E5_DIR false
#define INVERT_E6_DIR false
#define INVERT_E7_DIR false
#define X_HOME_DIR -1
#define Y_HOME_DIR -1
#define Z_HOME_DIR -1
#define X_BED_SIZE 102
#define Y_BED_SIZE 98
#define X_MIN_POS 0
#define Y_MIN_POS 0
#define Z_MIN_POS 0
#define X_MAX_POS X_BED_SIZE
#define Y_MAX_POS Y_BED_SIZE
#define Z_MAX_POS 9000
#define MIN_SOFTWARE_ENDSTOPS
  #define MIN_SOFTWARE_ENDSTOP_X
  #define MIN_SOFTWARE_ENDSTOP_Y
  #define MIN_SOFTWARE_ENDSTOP_I
  #define MIN_SOFTWARE_ENDSTOP_J
  #define MIN_SOFTWARE_ENDSTOP_K
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

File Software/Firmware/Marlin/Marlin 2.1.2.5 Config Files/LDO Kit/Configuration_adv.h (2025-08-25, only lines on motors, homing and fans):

#define E0_AUTO_FAN_PIN PC7 //LDO
#define E1_AUTO_FAN_PIN -1
#define E2_AUTO_FAN_PIN -1
#define E3_AUTO_FAN_PIN -1
#define E4_AUTO_FAN_PIN -1
#define E5_AUTO_FAN_PIN -1
#define E6_AUTO_FAN_PIN -1
#define E7_AUTO_FAN_PIN -1
#define CHAMBER_AUTO_FAN_PIN -1
#define COOLER_AUTO_FAN_PIN -1
#define HOMING_BUMP_MM      { 5, 5, 2 }       // (linear=mm, rotational=°) Backoff from endstops after first bump
#define HOMING_BUMP_DIVISOR { 2, 2, 4 }       // Re-Bump Speed Divisor (Divides the Homing Feedrate)
#define HOMING_BACKOFF_POST_MM { 10, 10, 10 }  // (linear=mm, rotational=°) Backoff from endstops after homing
#define MICROSTEP_MODES { 16, 16, 16, 16, 16, 16 } // [1,2,4,8,16]
#define ADVANCED_PAUSE_FEATURE
  #define ADVANCED_PAUSE_PURGE_FEEDRATE        3  // (mm/s) Extrude feedrate (after loading). Should be slower than load feedrate.
  #define ADVANCED_PAUSE_PURGE_LENGTH         50  // (mm) Length to extrude after loading.
  #define ADVANCED_PAUSE_RESUME_PRIME          0  // (mm) Extra distance to prime nozzle after returning from park.
    #define X_CURRENT       450        // (mA) RMS current. Multiply by 1.414 for peak current.
    #define X_CURRENT_HOME  X_CURRENT  // (mA) RMS current for homing. (Typically lower than *_CURRENT.)
    #define X_MICROSTEPS     16        // 0..256
    #define Y_CURRENT       450
    #define Y_CURRENT_HOME  Y_CURRENT
    #define Y_MICROSTEPS     16
    #define Z_CURRENT       800
    #define Z_CURRENT_HOME  Z_CURRENT
    #define Z_MICROSTEPS     16
    #define E0_CURRENT      800
    #define E0_MICROSTEPS    16
  #define X_HYBRID_THRESHOLD     100  // [mm/s]
  #define X2_HYBRID_THRESHOLD    100
  #define Y_HYBRID_THRESHOLD     100
  #define Y2_HYBRID_THRESHOLD    100
  #define Z_HYBRID_THRESHOLD       3
  #define Z2_HYBRID_THRESHOLD      3
  #define Z3_HYBRID_THRESHOLD      3
  #define Z4_HYBRID_THRESHOLD      3
  #define I_HYBRID_THRESHOLD       3  // [linear=mm/s, rotational=°/s]
  #define J_HYBRID_THRESHOLD       3  // [linear=mm/s, rotational=°/s]
  #define K_HYBRID_THRESHOLD       3  // [linear=mm/s, rotational=°/s]
  #define U_HYBRID_THRESHOLD       3  // [mm/s]
  #define V_HYBRID_THRESHOLD       3
  #define W_HYBRID_THRESHOLD       3
  #define E0_HYBRID_THRESHOLD     30
  #define E1_HYBRID_THRESHOLD     30
  #define E2_HYBRID_THRESHOLD     30
  #define E3_HYBRID_THRESHOLD     30
  #define E4_HYBRID_THRESHOLD     30
  #define E5_HYBRID_THRESHOLD     30
  #define E6_HYBRID_THRESHOLD     30
  #define E7_HYBRID_THRESHOLD     30
  #define SENSORLESS_HOMING // StallGuard capable drivers only
    #define X_STALL_SENSITIVITY  50
    #define X2_STALL_SENSITIVITY X_STALL_SENSITIVITY
    #define Y_STALL_SENSITIVITY  50
    #define Y2_STALL_SENSITIVITY Y_STALL_SENSITIVITY
    #define Z_STALL_SENSITIVITY  255

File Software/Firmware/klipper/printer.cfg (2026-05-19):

# Baby Belt Pro 
# This config is based off the parts in the Fabreeko Kit.
# if your self sourced, there will need to be additional tuning 
# Last Modified: 2025-10-22

[include boards/BTT_SKR_E3_V3.cfg]
[include boards/RPI.cfg]
[include mainsail.cfg]
[include macros.cfg]
[virtual_sdcard]
path: ~/printer_data/gcodes

#[include options/loop_prints.cfg] # Uncomment this to enable M808 for loop printing (Loop Count in KiriMoto, add M808 L<number of ADDITIONAL prints> to startup gcode and M808 to end gcode in ideamaker) 
#[include options/ignore_bed_heater_commands.cfg] # Uncomment this if you have remove/commented out the bed heater.  This will allow bed heater commands from your slicer to be ignored.
#[include options/angle_switch.cfg] # Uncomment if using the 30/45 degree angle_switch 
#[include options/BTT_TFT35.cfg] # Uncomment if using the stock Screen (BigTreeTech TFT35)
#[include options/BTT_SFS_V2_MOTION.cfg] # Uncomment to enable the motion sense feature of the BTT Smart filament Sensor V2
#[include options/BTT_SFS_V2_SWITCH.cfg] # Uncomment to enable the filament loaded feature of the BTT Smart filament Sensor V2
#[include options/Y_OFFSET.cfg] # Uncomment to enable the Y Offset calibration macros
#[include options/Z_BELT_RELEASE.cfg] # Uncomment to enable automatic Z-axis belt release at startup
#if using the KlipperScreen BTT PiTFT50 or other BTT PiTFT Screen, copy the KlipperScreen.conf to your config folder

[force_move]
enable_force_move: True

[printer]
kinematics: cartesian
max_velocity: 300
max_accel: 3000
max_z_velocity: 5
max_z_accel: 100  
 
[stepper_x]
step_pin: X_STEP
dir_pin: X_DIR
enable_pin: !X_ENABLE
microsteps: 16
rotation_distance: 32
endstop_pin: tmc2209_stepper_x:virtual_endstop
position_endstop: 0
homing_retract_dist: 0
position_max: 102
homing_speed: 25

[tmc2209 stepper_x]
interpolate: False
uart_pin: STEP_UART
tx_pin: STEP_TX
uart_address: 0
run_current: 0.21
diag_pin: ^X_DIAG
driver_SGTHRS: 50 # 255 is most sensitive value, 0 is least sensitive

[stepper_y]
step_pin: Y_STEP
dir_pin: Y_DIR
enable_pin: !Y_ENABLE
microsteps: 16
rotation_distance: 32
endstop_pin: tmc2209_stepper_y:virtual_endstop
homing_retract_dist: 0
position_min: -7.5
position_max: 105
homing_speed: 25
position_endstop: 0

[tmc2209 stepper_y]
interpolate: False
uart_pin: STEP_UART
tx_pin: STEP_TX
uart_address: 2
run_current: 0.25
diag_pin: ^Y_DIAG
driver_SGTHRS: 30 # 255 is most sensitive value, 0 is least sensitive

[stepper_z]
step_pin: Z_STEP
dir_pin: Z_DIR
enable_pin: !Z_ENABLE
microsteps: 16
rotation_distance: 8.6553
endstop_pin: tmc2209_stepper_z:virtual_endstop
position_endstop: 0.0
homing_retract_dist: 0
position_max: 999999
position_min: -15

[tmc2209 stepper_z]
interpolate: False
uart_pin: STEP_UART
tx_pin: STEP_TX
uart_address: 1
run_current: 0.3
diag_pin: ^Z_DIAG
stealthchop_threshold: 999999
driver_SGTHRS: 255  # 255 is most sensitive value, 0 is least sensitive

[extruder]
step_pin: E_STEP
dir_pin: E_DIR
enable_pin: !E_ENABLE
microsteps: 16
gear_ratio: 3:1
rotation_distance:  23.356048
nozzle_diameter: 0.400
filament_diameter: 1.750
max_extrude_only_velocity: 60
max_extrude_only_distance: 500
max_extrude_cross_section: 50
heater_pin: E_HEATER_PIN
sensor_type: Generic 3950 #EPCOS 100K B57560G104F
sensor_pin: E_SENSOR_PIN
control: pid
pid_Kp: 21.527
pid_Ki: 1.063
pid_Kd: 108.982
min_temp: 0
max_temp: 300

[tmc2209 extruder]
interpolate: False
uart_pin: STEP_UART
tx_pin: STEP_TX
uart_address: 3
run_current: 0.45

stealthchop_threshold: 999999

[homing_override]
axes: xyz
set_position_y: 25
gcode:
  {% set home_all = 'X' not in params and 'Y' not in params and 'Z' not in params %}
  {% set x_mid = printer.toolhead.axis_maximum.x/2|float %}
  #{% set fuzz = range(-10, 11) | random %}							# Add +/-10mm to X axis value for middle of bed
  {% set fuzz = 0 %}												# Add 0mm of to X axis value for middle of bed
  {% if "y" not in printer.toolhead.homed_axes %}
    G91                    # Relative Mode  
    G1 Y10 F500            # Try to move Y 10 mm away from the bed for good measure
    G90                    # Absolute Mode
  {% endif %}
  {% if home_all or 'X' in params %}
    G28 X                  # Home X first, because we want to be able to go to hit a point on the bed
    #{action_respond_info("homing_override fuzz Coord(x={0})".format(x_mid+fuzz))}
    G0 X{x_mid+fuzz} F2000           # Move to the middle of the bed with added fuzz range
  {% endif %}
  {% if home_all or 'Y' in params %}
    _SET_HOMING_CURRENT CURRENT=.20
    G28 Y 
    # Move back a bit away from the hard-stop immediately after homing
    G91             # Set to Relative positioning
    G1 Y10 F2000     # Move Y forward 5mm away from the edge
    G90             # Set back to Absolute positioning
    _RESTORE_RUN_CURRENT 
    SET_GCODE_OFFSET Y=0.0 # Start at 0.0 and adjust negative for squish on printer bed
  {% endif %}
  {% if home_all or 'Z' in params %}
    G28 Z    
  {% endif %}

[heater_bed]
heater_pin: BED_HEATER_PIN
sensor_type: Generic 3950  #ATC Semitec 104GT-2
sensor_pin: BED_SENSOR_PIN
control: pid
pid_Kp: 54.027
pid_Ki: 0.770
pid_Kd: 948.182
min_temp: 0
max_temp: 130

[heater_fan heatbreak_cooling_fan]
pin: FAN1
heater: extruder
heater_temp: 50.0
fan_speed: 1.0

[fan]
pin: FAN0

[mcu]
#serial: /dev/serial0 #UART option 1
#serial: /dev/ttyAMA0 #UART option 2 (if serial0 isn't mapping to ttyAMA0)
# Yours will be different, after flashing your firmware run the following command to find what your USB Serial ID is 
# ls /dev/serial/by-id/
#serial: /dev/serial/by-id/usb-Klipper_stm32g0b1xx_4B00170013504B5735313920-if00 #USB
restart_method: command

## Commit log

2023-08-12 Add files via upload
    This is an alpha, not fully tested.
    [BBPro_PrintBeltTention_36.stl, BBPro_PrintBeltTention_mirror_36.stl, BBPro_RightSide_25.stl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]
2023-08-16 Add files via upload
    New files
    [PrintBeltTention2x.stl, RightSide.stl, RightSide_MIR.stl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]
2023-08-29 Beta, file org, set notes and pos
    [BBPro-Scraper-withbagmountsr(Optional-replacesScraper).stl, BBPro-scraper.stl, BBPro_Nema17-ZGear.stl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]
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2023-10-20 Re-orient sides for proper printing
    [BBPro_Side-A.stl, BBPro_Side-B.stl]
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2023-11-03 Added Bamboo Option, Cleat and Mount Options
    Mount and Cleat options not 100% tested.
    [BBPro-Scraper-Mount(Optional).stl, BBPro-Scraper-withbagmounts(Optional-replacesScraper).stl, BBPro-Screen NoScreenbase-NEEDSUPPORT(Optional).stl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]
2023-11-23 updates to Marlin and profile stuff
    [printer.cfg]
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2023-12-28 Z drive gear and X car update
    Z drive no longer needs supports, X car is now one piece and easier to assemble.
    [BBPro_Roller-ZGear.stl, Xcarcombo.stl]
2023-12-28 Updated names on old files. Will make an old version branch when done
    [XcarA-LEGACY-DO-NOT-USE.stl, XcarB-LEGACY-DO-NOT-USE.stl]
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2024-04-30 Init Release ProV2
    First Release of Pro V2 New STLs, Profiles. Need to upload new STLs
    [BBPro-Screen-NeedsSupports.stl, BBPro-scraper.stl, BBPro_PrintBeltT-Frame-2x.stl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]
2024-05-31 Updated STRONGER print belt frames
    [BBPro_PrintBelt-Frame-update.stl]
2024-06-16 update firmware and profile stuff
    [printer.cfg]
2024-07-29 Updated Y Car for more bolt compatiblilty.
    [BBPro_Bamboo_YCarSide_A.stl]
2024-07-29 Update sides
    update BBPro Side A and B, For better Underbed, longer Nema 17, and less likely to crack Pi SD Card.
    [BBPro_Side-A.stl, BBPro_Side-B.stl]
2024-07-29 Add files via upload
    for new sides, much stiffer
    [BBPro_underbed.stl]
2024-08-27 Updated for better switch
    [BBPro_Side-B.stl]
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2024-08-27 Update BBPro_Side-B.stl
    Fixed, A and B are confusing? Ops!
    [BBPro_Side-B.stl]
2024-08-27 Update BBPro_Side-B.stl
    positioned right
    [BBPro_Side-B.stl]
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2024-10-10 removed duplicate of old files
    [BBProV2r1_RightSide_1.stl, BBProV2r1_RightSide_MIR_2.stl]
2024-11-04 fixing again dup and wrong files.
    [BBProV2r1_Xcar_MIR_14.stl, BBProV2r1_XrailMount_24.stl, BBProV2r1_XrailMount_MIR_23.stl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]
2024-11-06 more cleanup, getting ready for push to main.
    [BBProV2r1_SecondRailReplace_22.stl, BBProV2r1_scraper_25.stl]
2024-11-08 Added cleat and alignment tool
    [BBPro-FrenchCleat.stl, bbproXRailSpacerV2(printTwo).stl]
2024-11-16 Updated slice profile KM + KlipperCFG
    [printer.cfg]
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2025-01-07 Initial Documentation for Klipper *WIP*
    [Klipper Screen Mount.stl, Screen Cartridge - BTT PI TFT50 v2 cover.stl, macros.cfg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]
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2025-01-14 Update Klipper Screen Mount.stl
    fixed print orientation.
    [Klipper Screen Mount.stl]
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2025-01-22 move to Pin Aliases version of Klipper's printer.cfg to allow for different boards to be used. Re-arrange file/folder structure for Klipper Add "Announcement" Messages for options that are selectable.
    [BTT_SKR_E3_V3.cfg, BTT_TFT35.cfg, BTT_TFT35_menu.cfg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]
2025-01-22 add BTT SKR PICO to Board Options
    [BTT_SKR_PICO.cfg]
2025-01-22 Add a comment to SKR PICO Board pins file to explain why the fan numbers don't match
    [BTT_SKR_PICO.cfg]
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2025-02-02 Fix carriage return missing for uart links
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2025-02-14 all files uploading plz
    [BBPro-FrenchCleat.stl, BBPro-Scraper-Mount.stl, BBPro-Scraper-withbagmounts.stl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]
2025-02-25 updated files from zip
    [BBPro-FrenchCleat.stl, BBPro-Scraper-Mount.stl, BBPro-Scraper-withbagmounts.stl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]
2025-02-27 Adding in the BigTreeTech SFS 2.0 Mount and Documentation
    [BTT SFS v2 Mount.stl, BTT_SFS_V2_MOTION.cfg, BTT_SFS_V2_SWITCH.cfg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]
2025-05-29 Update to add User Mods Folder Add Locking Y Tensioner Nut to User mods from Madeline Add MMU&AMS Folder for Y Gantry with an MMU Painted version of the Linear Rail Replacement
    [BBProV25fl_LinearRailReplacement-MMU Painted Text.3mf, BBProV2_RockMonsterNo1YTentionerNut Locking.3mf, BBProV2_RockMonsterNo1YTentionerNut Locking.step]
2025-07-01 fix wire gauge documentation on degree sensor switch
2025-07-01 Add Marlin 2.1.2.5 Configuration Files Fix Links to STLS on TFT50.md page
    [Configuration.h, Configuration_adv.h]
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2025-07-30 Create CAD folder Add Step File for French Cleat Mount Move Step files into new CAD folder
    [frenchCleatMount.stp]
2025-08-25 LDO Kit files! Housekeeping new Change Log
    [Configuration.h, Configuration_adv.h, LDO Kit - Toolboard Mount v1.stl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]
2025-09-18 Create LDO-printer.cfg Update macros.cfg to fix issues with CANCEL_PRINT and PRIME_RIGHT
    [LDO-printer.cfg, macros.cfg]
2025-09-29 add md printed parts guide
    Creating a generic printed parts guide with pictures. Inspired by the legacy build guide's table.
    [printed_parts_md_builder.xlsx]
2025-09-29 fix images links
    [printed_parts_md_builder.xlsx]
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2025-09-29 add frame side B image
    [printed_parts_md_builder.xlsx]
2025-09-29 correct material recommendations
    [printed_parts_md_builder.xlsx]
2025-10-18 Add temp monitoring to SKR
    [BTT_SKR_E3_V3.cfg]
2025-10-22 Added ECAS files
    Added ECAS files for LDO kit or alternate style.
    [[a]_BBProV25fl_YCar_Bam_SideA_ECAS.stl, [a]_BBProV25fl_YCar_Bam_SideB_ecas-Looser.stl, [a]_BBProV25fl_YCar_Bam_SideB_ecas-Tight.stl]
2025-10-22 Add offset calibration tooling
    [95mm_wide_flat_test.stl, Y_OFFSET.cfg]
2025-10-22 enhance homing_override for individual axis control
    [printer.cfg]
2025-10-22 Add rpi temp and new optional macro to template
    [printer.cfg]
2025-10-22 Remove irrelevant code from belt printer
    [macros.cfg]
2025-10-22 update print_start
    consistent 2 space indentation
    [macros.cfg]
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2025-10-22 indentation and consistent relative/absolute mode control
    [macros.cfg]
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2025-10-22 split cancel_print from print_end
    [macros.cfg]
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2025-10-22 fix for VALIDATE_ANGLE
    [macros.cfg]
2025-10-22 fix to validation handling
    [macros.cfg]
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2025-10-23 Revert "z belt release"
    This reverts commit 55418e750addab031fbc03a77de3912c313f5143.
    [Z_BELT_RELEASE.cfg, printer.cfg]
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2025-10-26 add safe_extrude and swap to nozzle_prime
    [macros.cfg]
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2025-10-26 both klipper and ellis3d advise against hold_current
    https://ellis3dp.com/Print-Tuning-Guide/articles/determining_motor_currents.html#determining-hold_current
    [printer.cfg]
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2025-11-14 Update angle_switch.cfg
    replace prime_right in angle_switch.cfg w/ nozzle_prime
    [angle_switch.cfg]
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2026-04-28 add kirimoto klipper profile, guide, macros
    Add kilpper profile and supporting macros/docs for KiriMoto. Fix build guide typo. add 1mm moves to yoffset macros.
    [LDO-printer.cfg, Y_OFFSET.cfg, loop_prints.cfg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]
2026-04-29 document loop printing, fix y offset 1mm macros
    [LDO-printer.cfg, Y_OFFSET.cfg, ignore_bed_heater_commands.cfg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]
2026-05-07 Init Release of 2.6
    BBPro 2.6 Init Release - Beta, this may need to be changed.
    [BBProV25fl_LinearRailReplacement-MMU Painted Text.3mf, BBProV25fl_X-Carraige.stl, BBProV26fl_LinearRailReplacement.stl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]
2026-05-08 2.6 part orientation fixes
    [BBProV26fl_X-CarraigeMotorMount.stl, [a]_BBProV25fl_RockMonsterNo1YTentionerIdlerHolder.stl, [a]_BBProV26fl_RockMonsterNo1YTentionerBody.stl]
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2026-05-18 adjust printer.cfgs
    setting homing_retract_dist on y to 0 to get rid of "Endstop stepper_y still triggered after retract" errors. moved the Y +10mm move into the homing macros. When the printer hits the end of the axis, it registers the stall, stops, and immediately tries to pull away by 10mm. Klipper interprets that sudden acceleration change to back away as a second "crash," throwing the error.
    [LDO-printer.cfg, printer.cfg]
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2026-06-21 v2.6 document updates
    rework gantry install doc for v2.6
2026-06-22 Printed parts guide update for 2.6
    update printed parts guide for 2.6, add indicator to filename for parts needing heat sets. TODO - new part pictures.
    [[ai]_BBProV26fl_XrailMountUnder-SideA.stl, [ai]_BBProV26fl_XrailMountUnder-SideB.stl, [i]_BBProV26fl_X-Carraige.stl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]

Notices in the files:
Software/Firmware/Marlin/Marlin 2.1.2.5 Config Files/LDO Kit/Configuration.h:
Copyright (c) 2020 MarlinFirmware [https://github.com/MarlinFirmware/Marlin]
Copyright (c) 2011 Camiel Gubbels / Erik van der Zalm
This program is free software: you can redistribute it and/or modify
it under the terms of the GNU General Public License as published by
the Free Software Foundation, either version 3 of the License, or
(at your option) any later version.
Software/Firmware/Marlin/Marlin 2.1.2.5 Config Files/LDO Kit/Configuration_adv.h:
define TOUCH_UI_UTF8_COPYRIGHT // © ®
